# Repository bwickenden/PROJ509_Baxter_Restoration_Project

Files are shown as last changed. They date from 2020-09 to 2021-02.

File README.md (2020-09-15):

# Baxter Restoration Project

This project is to restore the Baxter robot at the University of Plymouth, to be used for research and teaching purposes. The project uses Autodesk Fusion 360 to design and tests a new gripper to repair the end effector of the Baxter robot. A Kinematics model for the Baxter has been produced, which includes both forward and inverse kinematics to be used to control the robot. Both of these systems have been used in MATLAB, with demonstrations being shown in the video folder. A Gazebo 7 simulation of the Baxter Robot was also tested during this project. The test programmes used were provided by Rethink Robots, and was used in their simulation environment. 

## MATLAB
All of the MATLAB files that have been used in the project have provided in the MATLAB folder. For all of the simulations, the vars.m and simulation.m files need to ran first. Examples of forwards, inverse kinematics and semaphore signalling are provided. 

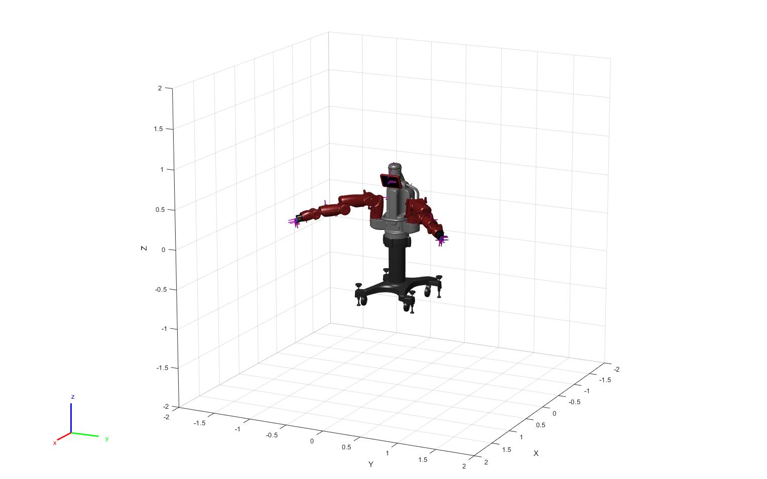
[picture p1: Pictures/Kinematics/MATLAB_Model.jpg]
MATLAB Baxter Model


## CAD

Two models for the grippers have been produced for this project. A design for both 3D printed ABS/PLA and for Aluminium has been provided. Each design has been through a sereis fo FEA tests, which concluded that each design (with its respected materials) has a minimum factor of safey above the target goal of 5. The project and stl files have beeen provided for both models. 

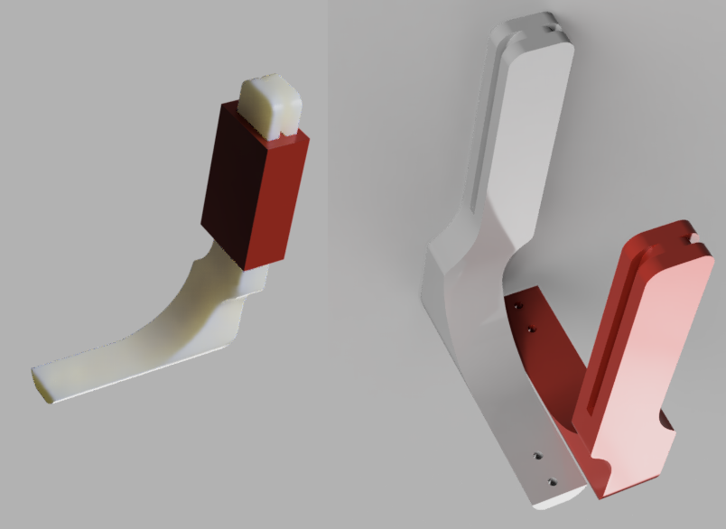
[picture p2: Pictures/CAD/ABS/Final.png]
ABS

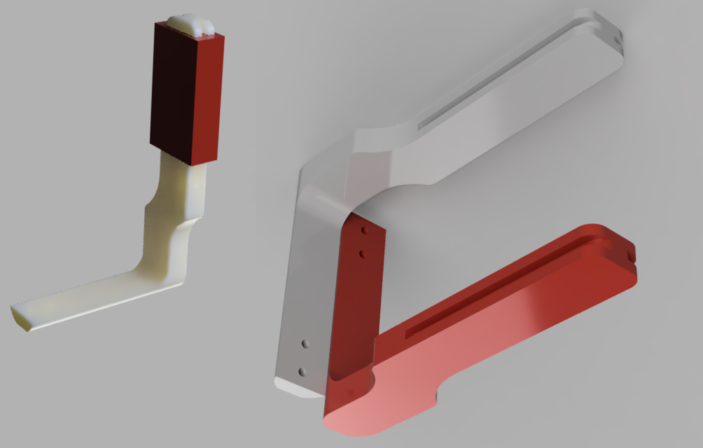
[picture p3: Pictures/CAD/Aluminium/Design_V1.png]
ALU


## ROS

Due to Rethink Robotic's workstation and  Gazebo 7 simulation using legacy software, changes has to be made to the setup of the workstation in order to get it working on Ubuntu 16.04 using ROS Kinetic. 

To set up the workstation the wiki provided by Rethink was followed and adapted. The original guide can be found at https://sdk.rethinkrobotics.com/wiki/Workstation_Setup  and the simulator guide can be found here https://sdk.rethinkrobotics.com/wiki/Simulator_Installation 

As a prerequisite an installation of Ubuntu 16.04 with ROS Kinetic is required. And to have 

### Install the SDK for Baxter 
$ cd ~/ros_ws/src
$ wstool init .
$ wstool merge https://raw.githubusercontent.com/RethinkRobotics/baxter/master/baxter_sdk.rosinstall
$ wstool update
$ source /opt/ros/kinetic/setup.bash

$ cd ~/ros_ws
$ catkin_make
$ catkin_make install

$ wget https://github.com/RethinkRobotics/baxter/raw/master/baxter.sh
$ chmod u+x baxter.sh

$ cd ~/ros_ws
$ gedit baxter.sh

In the baxter.sh file, in order for the workstation to be used within a simulation the baxter_hostname has to set to “my_computer.local”, however if the user wants to interact with the physical Baxter robot rather than the simulation, the variable “your_ip” needs to be set to the workstations ip address. Additionally, the variable of ros_version, needs to be set to “kinetic.

$ cd ~/ros_ws
$ . baxter.sh

After this the Simulator can be installed. 
With the simulaor setup a variety of test programmes can be used to experiment with

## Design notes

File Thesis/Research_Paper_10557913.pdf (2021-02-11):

## Restoration of the Baxter Robot for Research and Teaching

Benjamin Wickenden

The University of Plymouth Benjamin.wickenden@postgrad.plymouth.ac.uk

Abstract

This paper covers the restoration of the Baxter Robot project at the University of Plymouth, which ended in 2016. This includes an in-depth look into the Baxter robot and surrounding field, which incorporates topics such as teleoperation, robot-human interaction, robotics arms, industrial robotic and domestic-home robotics. As part of the Baxter robot’s restoration a replacement end effector has been designed using Autodesk Fusion 360. The design underwent a series of structural analysis tests in the form of finite element analysis (FEA) simulation software, which concluded that the models designed could endure the stress testing, whilst retaining a factor of safety above five. A simulation in MATLAB is used to show the full range of Baxter’s arms in 3D. Additionally, a 2D representation can be seen, mapping all the possible end effector positions of one of Baxter’s arms. Additionally, the inverse kinematics are also derived and demonstrated in a simulation in MATLAB. The project also used the Rethink Robotics ROS Baxter robot simulator carry out interactive testing with the Baxter robot using the keyboard. Lastly, an interactive programme in MATLAB was used to carry out semaphore signalling, which was used to spell out Baxter, when the user inputted the characters. The paper then concludes that the Baxter robot retains a lot of value for research and teaching purposes and that the project provides a starting point for future projects to continue from.

Keywords

Baxter, Kinematics, Semaphore signalling, MATLAB, Simulation, Autodesk Fusion 360, Finite Element Analysis (FEA), Human-Robot Interaction, Industrial Robotics

### 1. Introduction

The overall focus of this project is the restoration of the University of Plymouth’s Baxter Robot (Robots IEEE, 2020a), which has been out of use since 2014 and due to researcher’s departure and damage sustained. The Baxter robot is designed to for a variety of purposes including object identification, light assembly, material handling. The Baxter robot has two industrial robotic arms with 7 degrees of freedom each, with compliant joints which have force sensing capabilities, a 360o
-sonar detection
sensor, and 3 cameras (Rethink Robotics, 2012). The University’s Baxter robot has a damaged end effector which needs replacing and requires, software to be provided to interact with the robot in order for future research to be carried out. Therefore, the overall goal of this project is to restore the Baxter project to the point where research using the robot can once again take place at the University of Plymouth.

The first objective involves designing a new replacement end effector which can be 3D printed and fitted to Baxter robots’ arm. Autodesk Fusion 360 was used to create 3D CAD models of the end effectors grippers, and to carry out structural analysis on the models in the form of finite element analysis (FEA) which provided me a level of confidence with my design when experiencing extreme forces. The second objective involves creating an environment with MATLAB and ROS where a physical and mathematical model of the Baxter Robot is present and ready for testing. Which includes providing instructional documentation for installing Rethink Robotics simulator, which uses legacy software, on the University’s system. Additionally, for the MATLAB aspect of this objective, the focus is on providing the kinematics of the Baxter robots arm and the robots parameters. Objective three is focused on using MATLAB and ROS to interact with the Baxter robot. In ROS, the goal is to interact with Baxter’s arms in a Gazebo 7 simulation and the MATLAB implementation to focus on demonstrating the kinematics of the Baxter using the MATLAB robotics toolbox and to provide an interactive semaphore signalling simulation. Lastly the fourth objective is to provide additional project ideas and uses for the Baxter robot to be used in future research projects at the University of Plymouth.

The code for both the MATLAB and the ROS simulations that were carried out during the project can be found on the projects GitHub repository: https://github.com/bwickenden/PROJ509_Baxter_Restoration_Project.git along with other documentation and results. The ROS simulations were carried out in a virtual machine boot of Ubuntu 16.04, using ROS Kinetic and the MATLAB simulations were running of MATLAB R2020a.

### 2. Background Literature

### 2.1. Industrial Robots

In 2015, Rethink Robotics released the Sawyer robot, which was the successor of Baxter (Robots IEEE, 2020b). The Sawyer robot has a singular industrial robotic arm with seven degrees of freedom and has two integrated cameras, along with built in force sensing capabilities (Rethink Robotics, 2019a). Sawyer is designed to carry out pick and place tasks as well as specific manufacturing task such as CNC machining, injection moulding, circuit board assembly, and packing, along with many other tasks (Rethink Robotics, 2019b). With Sawyer’s force sensing capabilities, it allows Sawyer to carry out task carefully, by monitoring both the torque and position of each of its servos individually and simultaneously (Rethink Robotics, 2019c). By doing this it allows the robot to monitor and control the amount of force that it is applying to its target. With this ability, the Sawyer robot is able to carry out tasks within a sensitive environment, where a regular industrial robot arm, without force feedback capabilities would not be able to operate within safely. This is a similar trait that the Sawyer robot shares with its predecessor, the Baxter robot, that also made use of compliant joints with force sensing, to operate within its environment safely (Rethink Robotics, 2012). One difference between Sawyer and Baxter robot is that the Sawyer robot is less bulky and is instead flexible and streamlined to enough to work in environments which may be difficult for its human counterparts to operate within (Rethink Robotics, 2019a). This is achieved with the application of Rethinks Robotics’ Inertia Software and advanced embedded vision system, which allows for the Sawyer robot to reorient its position into a dynamic pose to suit the operational environment (Rethink Robotics, 2019b).

### 2.2. Cooking Robots

In a research study carried out by Zhai, J. et al., (2015) they simulated a dual arm, 6 degree of freedom robot to carry out Chinese cooking methods, with the idea of providing quality dishes autonomously, without the need of a master chef. In the paper, they focus on the action required to flip food within a wok, which is achieved with the use of inverse kinematics and dynamic equations, which are provided by the Lagrangian method, which calculates the Kinect and potential energy of the arms. In a study ran by Petit, A, et al., (2017), they were able to train a robot to make a pizza. This was achieved by using an RGB-D 3D camera to create a point cloud, which enables the robot to track elastic deformable objects that are textured, such as pizza dough. The unique aspect of this research is that unlike other research projects this deals with handling non-rigid objects, whereas most research appears to be in the handling of rigid tools.

### 2.3. Human-Robot Interaction

In a study carried out by Li, C. et al., (2020) they used force sensing with a KUKA LBR iiwa robotic arm to provide a massage to the user. The idea behind the project was to provide the service without the need of a person being present and to design a system that would allow for the robot to provide the massage dynamically to suit different users. With the robot being able to autonomously complete its tasks without being controlled by another person, it allows for the robot to be applied to a home robotics setting, such as a smart home. Whilst a massage for many is a luxury, for some people it may be required due to healthcare reasons and therefore this provides an important solution to this service.

### 2.4. Teleoperation

One example of teleoperation is using robots to work from home; this is achieved by a company in Japan called OryLaboratory, which has created a service robot that can be remotely controlled named the OriHime robot (OryLaboratory, 2020). In 2018 OryLaboratory conducted a trial in a café in Tokyo called Dawn Ver Café, where the service was provided by robots controlled by people with disabilities which prevented them working, via teleoperation with the goal of allowing them to remain independent (Steffen, 2020). The robot interface to control the OriHime robots has been designed to be interactable for people who have ALS and are paralyzed, which is achieved by the use of eye control, body language and simple gestures (OryLaboratory, 2020), (DAWN, 2020).

### 3. Theory

### 3.1. Kinematics

Both inverse and forwards kinematic were developed for the project. The main difference between inverse and forward kinematics is the control inputs. For inverse kinematics the user would input the target location and the model will produce the values for the joint angles in order for the pose of the robotic arm to position its end effector within the target location.
Forward kinematics allow for the
user to use the joint angles of the
robotic arm as the input controls, where the kinematic model is then used calculate the pose of the robot and the resultant location of the end effector within the environment. In figure 7, I have used MATLAB’s
robotics | toolbox | (MathWorks,
2020) to calculate all of the possible positions of the end effector within Baxter’s workspace using forwards kinematics as seen in Figure 1.

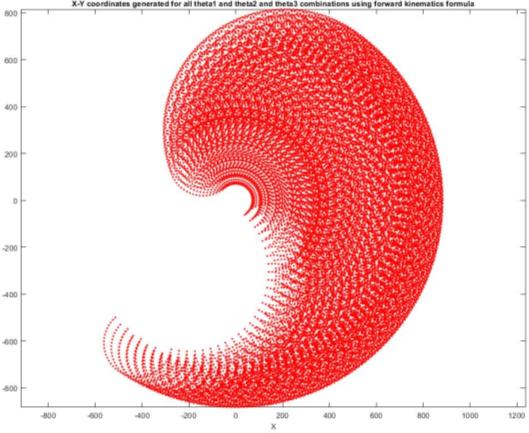
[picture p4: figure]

Figure 1: Baxter End effector range 2D

Similar to the forwards kinematics, the inverse kinematics (Equation 1) were also successfully demonstrated using a model of Baxter with MALAB, with the user inputting the target coordinates. Inverse kinematics are useful when integrated with an autonomous system, as they allow for the user to input the target location of the end effector and for the robot to provide a solution for the joint angles. However as discussed, over or undershoot may cause issue when using an open loop system with forwards kinematics, which is why a closed loop feedback system is preferred to maintain accuracy.

X =

Px
Py
φ

=

a1c2 + a2c12 + a3c123
a1s1 + a2s12 + a3s123
θ1 + θ2 + θ3

Equation 1: Where Px and Py represent the chosen x,y coordinate and a1,a2,a3 are lengths 1,2,3 with s and c representing sin and cos of angles 1,2,3

### 4. Design

### 4.1. CAD

The design for the replacement end effector offered different variants for the use of aluminium and ABS/PLA. Both designs are similar; however, the ABS/PLA design has more material added to provide a better distribution of force along the bend. There are two different designs due to the difference in the material properties between ABS and aluminium. ABS has a Youngs modulus of 1.1-2.9GPa when 3D printed (igem, 2015), whereas aluminium’s has a Young’s Modulus of 69Gpa of (The Engineering ToolBox, 2003). Both designs went through FEA with a force of 35N applied, where the results can be seen in Figure 2. The minimum factory of safety for the ABS/PLA design was 5.501, and the minimum factor of safety for the aluminium design with the same constraints and forces applied was 15, which more than exceeds target factor of safety of 5.

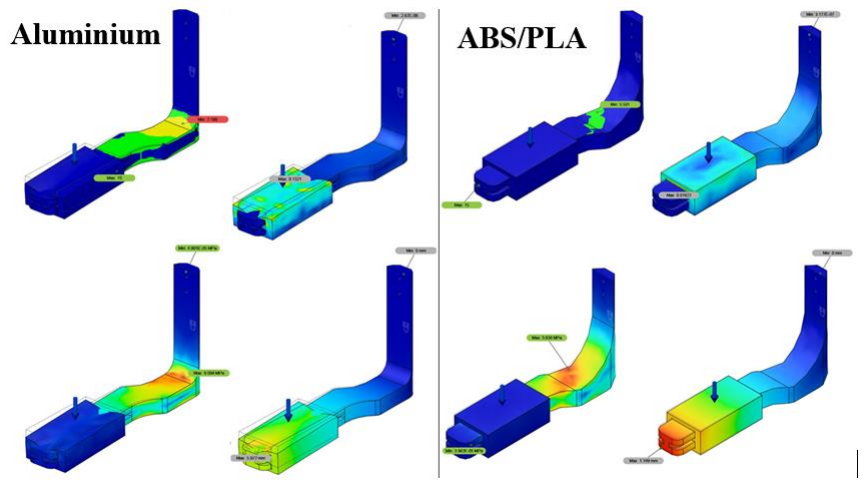
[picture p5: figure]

Figure 2: FEA Safety Factor (TL), Strain (TR), Stress (BL), Displacement (BR)

### 4.2. Semaphore Signalling

Semaphore signalling is a system designed by the Chappe brothers in the 18th century (Centre of Innovation in Mathematics Teaching, 2006) and is a method of using two flags to signal letters by the position of the user’s arms when holding the flags. Using the forwards kinematic model in MATLAB, an interactive programme was made, where the user could input the characters to spell Baxter, which results in Baxter producing the semaphore signal using his arms, seen in Figure 3.

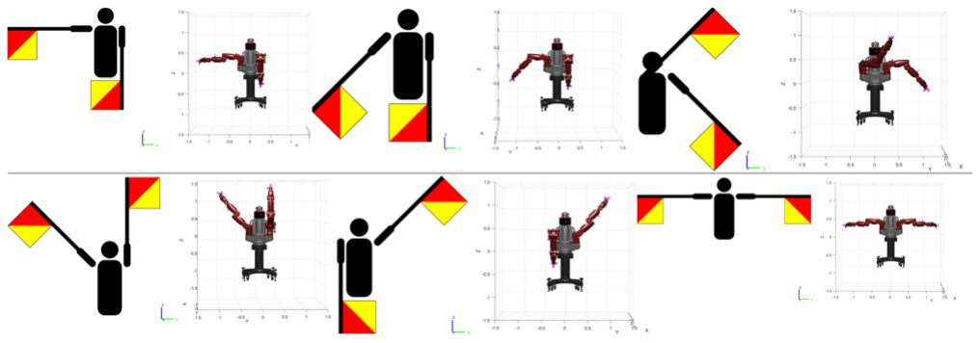
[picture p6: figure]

Figure 3: Semaphore signalling, Row 1: B, A, X. Row 2: T, E, R.

### 5. Discussion and Analysis

### 5.1. CAD

Whilst providing a structurally strong and stable part of a certain quality is important to ensure the grippers of the end effector will not require constant replacement; it is also important to consider the forces that would be applied to the rest of the robot if the end effector experiences a large impact force. With the Baxter robot’s servos costing more than a replacement gripper it is perhaps best to design the gripper to break at a predetermined threshold, which would allow for the gripper to be used within normal operation without issue, but would break when experiencing extreme force, in order to protect the servos and their gear boxes. Whilst ABS/PLA are cheaper materials that Aluminium, they are not suited to all scenarios. For example, with the print bed temperature being around 72⁰C for PLA (igem, 2015), PLA is not suited for use in hot environments. If the PLA gripper was to be used in a cooking environment, the gripper may experience damage due to heat, whereas the aluminium will be able to sustain more heat and may be better suited.

### 5.2. Kinematics

The kinematics derived and demonstrated within this project show examples of both forwards and inverse kinematics. For the purposes and scope of the project the kinematics are purely theoretical and demonstrated in a perfect system, and therefore don’t fully represent a real system. In a real system, such as using the kinematic model with the physical Baxter robot, the servos would not be perfect and therefore the location of the end effector within a 3D plane may experience some compound drift. Due to experiencing drift the certainty of the end effectors position would decrease, however a solution to this could be solved using a closed loop feedback control system. The implementation of a closed loop feedback control system can be used to increase the accuracy of the end effector by providing feedback data which will allow for adjustments to be made to the joint angles of the servos to reach the required goal. Several methods could be used as a solution this issue including a simple proportional-integral-derivative controller (PID controller) or a Kalman filter.

### 5.3. Interaction

The current semaphore signalling programme has Baxter produce the signals using his arms alone, without the use of flags. With access to Baxter, further research could be carried out with Baxter interacting with a set of signalling flags, where a project could be centred around using Baxter as a translator from variable or written commands to semaphore signalling. It is also possible that with the use of computer vision that Baxter could be taught to read semaphore signals, to then be used as input commands. In order to do this Baxter would need to make use of RBG-D camera to track the skeletal data of a user which could then be used with a machine learning programme to match the data with predetermined poses (Win, S. et al., 2020).

### 6. Conclusion and Future Work

In future I would like to carry out a series of tests using the actual Baxter robot to further the semaphore signalling system developed within the project. In a future study I would like to train the Baxter robot to recognise a semaphore signal and to be able to repeat the signal. This would be achieved with the use of a depth camera which could be used to carry out skeletal tracking of a human producing the signals. With the skeletal data recorded, the data could be converted to forwards kinematics for Baxter to replicate to reproduce the same signal. Baxter could also use the values of the joint angles to identify the semaphore signal, and thus translating the signal. A similar experiment was carried out using the pepper robot by Tian, N. et al., (2018), where they used cloud computing to mirror semaphore signals.

Due to Baxter’s compliant joints and with the use of torque sensors, which allow him to work safely with humans, Baxter has the possibility carry out cooking related tasks. Using machine learning and neural network applications, Baxter could complete kitchen tasks autonomously. A user can control Baxter via teleoperation to complete cooking tasks. This could be used in combination with a VR headset, allowing the user to see the environment fro m Baxter’s perspective (Lipton, J.I. et al., 2018). The user could then input movements using VR controllers in combination with Baxter’s torque force sensing to ensure that the appropriate force is being used to complete tasks such as cutting fruit or gripping a saucepan.

Overall, to conclude the project has successfully achieved its goals of restoring the Baxter robot project. Following the literature review of the Baxter robot and surrounding fields, it was concluded that Baxter has a lot of potential to be used for research into areas which involve robots-human interaction. It was also established that due to Baxter’s multidisciplinary potential, he also provides a valuable platform to teach students several applications of robotics. Future research into Baxter using semaphore signalling and completing cooking tasks looks promising. With the conclusion of the project, the first steps towards Baxter’s restoration have been completed, with a toolbox provided as a footing for future research to be conducted.

### 7. References

Centre of Innovation in Mathematics Teaching (2006) Semaphore. Available at: http://www.cimt.org.uk/resources/topical/semaphore/semaphore.htm.(Accessed: 13 September 2020).

DAWN (2020) Freedom for everyone to participate in society and work with their peers. Available at: https://dawn2019.orylab.com/ (Accessed: 13 September 2020).

igem | (2015) Comparison | of | typical | 3D | printing | materials. | Available | at:
http://2015.igem.org/wiki/images/2/24/CamJIC-Specs-Strength.pdf (Accessed: 13 September 2020).

Li, C. Fahmy, A. Li, S. and Sienz, J. (2020) “An Enhanced Robot Massage System in Smart Homes Using Force Sensing and a Dynamic Movement Primitive”. Front. Neurorobot. 14:30. doi: 10.3389/fnbot.2020.00030

Lipton, J. I. Fay, A. J. and Rus, D. (2018) "Baxter's Homunculus: Virtual Reality Spaces for Teleoperation in Manufacturing," in IEEE Robotics and Automation Letters, vol. 3, no. 1, pp. 179-186, Jan. 2018, doi: 10.1109/LRA.2017.2737046.

MathWorks (2020) Simulate Joint-Space Trajectory Tracking in MATLAB. Available at: https://uk.mathworks.com/help/robotics/examples/simulate-joint-space-trajectory-tracking.html.(Accessed: 13 September 2020).

OryLaboratory (2020) OriHime. Available at: http://ces15.orylab.com/ (Accessed: 13 September 2020).

Petit, A. Lippiello, V. Fontanelli, G. A. Siciliano, B. (2017) “Tracking elastic deformable objects with an RGB-D sensor for a pizza chef robot”, Robotics and Autonomous
Systems,Volume | 88,2017,Pages | 187-201,ISSN | 0921-
8890,https://doi.org/10.1016/j.robot.2016.08.023.
Rethink | Robotics | (2019a) | Applications. | Available | at:
https://www.rethinkrobotics.com/sawyer/applications#c68. (Accessed: 13 September 2020).
Rethink | Robotics | (2019b) | Sawyer | Black | Edition. | Available | at:
https://www.rethinkrobotics.com/sawyer. (Accessed: 13 September 2020).
Rethink | Robotics. | (2012) | 'Baxter | Datasheet'. | Available | at: | https://www.allied-
automation.com/wp-content/uploads/2015/02/Baxter_datasheet_5.13.pdf (Accessed: 10 April 2020).

Rethink Robotics. (2019c) ‘Rethink Robotics® meets German Engineering'. Available at: https://www.rethinkrobotics.com/fileadmin/user_upload/sawyer/rr-blackedition-brochure_low.pdf (Accessed: 13 September 2020).

Robots IEEE (2020a) Baxter. Available at: https://robots.ieee.org/robots/baxter/ (Accessed: 10 April 2020).

Robots IEEE (2020b) Sawyer. Available at: https://robots.ieee.org/robots/sawyer/. (Accessed: 13 September 2020).

Steffen, L. (2020) Café In Tokyo Uses Robot Waiters Controlled By Paralyzed People. Available at: https://www.intelligentliving.co/cafe-tokyo-robot-waiters-paralyzed-people/ (13 September 2020).

The Engineering ToolBox (2003) Young's Modulus - Tensile and Yield Strength for common Materials. Available at: https://www.engineeringtoolbox.com/young-modulus-d_417.html (Accessed: 13 September 2020).

Tian, N. et al., (2018) "A Cloud-Based Robust Semaphore Mirroring System for Social Robots," 2018 IEEE 14th International Conference on Automation Science and Engineering (CASE), Munich, 2018, pp. 1351-1358, doi: 10.1109/COASE.2018.8560553.

Win, S. and Thein, T. L. L. (2020) "Real-Time Human Motion Detection, Tracking and Activity Recognition with Skeletal Model," 2020 IEEE Conference on Computer Applications (ICCA), Yangon, Myanmar, 2020, pp. 1-5, doi: 10.1109/ICCA49400.2020.9022822.

Zhai, J. Pan, G. Yan, W. Fu, Z. and Zhao, Y. (2015) "Dynamic analysis of a dual-arm humanoid cooking robot," 2015 IEEE 10th Conference on Industrial Electronics and Applications (ICIEA), Auckland, 2015, pp. 835-838, doi: 10.1109/ICIEA.2015.7334226.

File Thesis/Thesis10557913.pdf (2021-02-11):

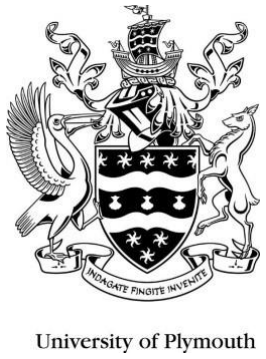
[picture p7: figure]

# Restoration of the Baxter Robot for use in Research and Teaching

# Benjamin Wickenden

### Supervisor: Dr M. Ambroze

## A thesis submitted to the University of Plymouth in partial fulfilment of the requirements for the degree of:

## Master of Science, Robotics

September 2020

School of Computing, Electronics, and Mathematics

Faculty of Science and Engineering

## Declaration

I confirm that I have read and understood the Plymouth University regulations relating to Assessment Offenses and that I am aware of the possible penalties for any breach of these regulations. I confirm that this is my own independent work.
Candidate's Signature:
<Benjamin Wickenden> | Date:13/10/2020

Supervisor's Signature:

<Dr Marcel Ambroze> | Date:

Second Supervisor's Signature:

<Dr Chunxu Li> | Date: 12/10/2020

Copyright & Legal Notice
This copy of the dissertation has been supplied on the condition that anyone who consults it is understood to recognize that its copyright rests with its author and that no part of this dissertation and information derived from it may be published without the author's prior written consent.

The names of actual companies and products mentioned throughout this dissertation are trademarks or registered trademarks of their respective owners.

## Abstract

This paper covers the restoration of the Baxter Robot project at the University of Plymouth, which ended in 2016. This includes an in-depth look into the Baxter robot and surrounding field, which incorporates topics such as teleoperation, robot-human interaction, robotics arms, industrial robotic and domestic-home robotics. As part of the Baxter robot’s restoration a replacement end effector has been designed in CAD using Autodesk Fusion 360. The design underwent a series of structural analysis tests in the form of Fusion 360’s built in finite element analysis (FEA) simulation software. The FEA testing provided an evaluation of the model which concluded that a suitable model had been produced to endure the full force of Baxter with a safety factor above five; with two different models produced, the material being 3D printed ABS, or machined Aluminium. The project also develops inverse and forward kinematics for Baxter’s arms. A simulation in MATLAB is used to show the full range of Baxter’s arms in 3D by cycling through joint angles for each of servos. Additionally, a 2D representation can be seen, mapping all of the possible end effector positions of one of Baxter’s arms. A model to demonstrate the inverse kinematics is also produced in a MATLAB simulation where the user can input the X,Y coordinates of a target location into the kinematic model which then calculates to joint angles of the servos in order for the end effector to reach its goal. The project also used the Rethink Robotics ROS Baxter robot Gazebo 7 simulation to perform interactive testing with the Baxter robot using the keyboard. Lastly, an interactive programme in MATLAB was used to carry out semaphore signalling, which was used to spell out Baxter, when the user inputted the characters. The paper then concludes that the Baxter robot retains a lot of value for research and teaching purposes and that the project provides a starting point for future projects to continue from.

## Acknowledgements

I would like to thank both Dr Ambroze and Dr Li, for their help and guidance throughout this project.

Additionally, I would also like to thank my house mates and family for their support throughout the project.

Lastly, I would like to thank all the Robotics technicians at the University of Plymouth for their time and help that they have generously provided me with throughout my time at the University.

## Contents

## 1. Introduction

The overall focus of this project is the restoration of the University of Plymouth’s Baxter Robot, which was first manufactured by Rethink Robotics in 2012 (Robots IEEE, 2020a). The University of Plymouth’s Baxter robot has been out of use since 2014 and due to researcher’s departure and damage sustained by Baxter. The Baxter robot has a damaged end effector which needs replacing and in addition, software needed to be provided to interact with the robot in order for future research to be carried out. Therefore, the overall goal of this project is to restore the Baxter project to the point where research, using the robot can once again take place at the University of Plymouth. In order to achieve this the project was broken down into four objectives.

- Design a replacement end effector for the Baxter Robot
- Have a working model of the Baxter Robot
- Provide working code to interact with the Robot
- Further experimentation

The first objective involves designing a new replacement end effector which can be printed and fitted to the Baxter robots’ arm. The main software used in the objective is Autodesk Fusion 360 which is used to create a 3D CAD model of the end effector, and is also used to carry out structural analysis on the model in the form of finite element analysis (FEA) which provided me a level of confidence with my design when experiencing extreme forces. The second objective involves creating an environment with ROS and MATLAB where a physical and mathematical model of the Baxter Robot is present and ready for testing. The ROS element of this objective also involves an instructional document which provides potential future researchers with a way to set up a ROS environment using the Rethink Robotics simulator legacy software on the University’s software requirements. For the MATLAB aspect of this objective, the focus is on providing the kinematics of the Baxter robots’ arm and the robots parameters. Objective three is focused on using ROS and MATLAB to interact with the Baxter robot. The ROS implementation involves controlling the robot’s arms in a Gazebo simulation and the MATLAB implementation to focus on demonstrating the kinematics of the Baxter robot using the MATLAB robotics toolbox. Lastly the fourth objective is to provide additional project ideas and uses for the Baxter robot to be used in future research projects at the University of Plymouth.

Due to the global pandemic of COVID-19, the direction of the project changed from its original objectives. Originally the project was to be more focused on running a full diagnostics test and repair on the University’s Baxter robot, followed up with the running of simple physical testing, which would include the robot interacting with the environment around it. However, due to the pandemic and the closure of the University’s campus on 16th March 2020, the goals and objectives of the project had to be adapted to compensate not having access to the robot and thus the project moved towards a theoretical and simulation based project, which places a greater emphasis on the literature and fields surrounding the Baxter robot.

Throughout the project, careful planning and management took place using a series of Gantt charts which allowed me to breakdown all my work packages into smaller, more manageable tasks. Over the duration of the project three iterations of the Gantt chart were produced. The original Gantt (Appendix 1), was produced pre-Covid-19 and outlined my original project plans before the University’s closure. Upon the closure of campus, the project plan was revaluated to match the new direction of the project. The new Gantt chart removed several tasks from the project plan as with the project being mainly theory based, some of the tasks were no longer possible and due to the circumstances, some tasks were no longer able to be realistically achieved within the time frame. In addition, the deadlines for work packages were pushed back by a week, due to unforeseen deadlines changes for semester two which meant that I started working on the project a week later than expected (Appendix 2). In this update of the Gantt chart I also changed how I staggered some of the tasks, by setting some tasks to run over a longer period in parallel to other tasks. This adaptation was made to allow me to work on related tasks simultaneously, which in practice helped greatly when it came to problem solving. The finial iteration of the Gantt chart is seen in (Appendix 3), which is updated due to the change in deadline, which allowed for a final adjustment of remaining tasks to be completed. The final Gantt chart is also a representation of how the project played out, rather than a forecast and therefore lends itself as a way to evaluate, time and project management skills, throughout the duration of the project.

The code for both the MATLAB and the ROS simulations that were carried out during the project can be found on the projects GitHub repository, along with video demonstrations and
CAD | files: | https://github.com/bwickenden/PROJ509_Baxter_Restoration_Project.git
Documentation on the project was also kept locally as well as on the OneDrive. The ROS simulations were carried out in a virtual machine boot of Ubuntu 16.04, using ROS Kinetic. In addition to formal documentation I also kept a paper journal which was used to planning tasks, note taking, rough mathematics and evaluation at the time of experimentation.

## 2. Literature Review

Abstract

In this literature review I will be looking into the current applications and research areas in relation to the Baxter robot focusing on areas of research and for teaching purposes. Following this, an analysis into the field surrounding the Baxter robot is carried out, starting with what other robots and robotic arms are available, that are within similar fields and scope of the Baxter robot. This paper then leads into an in-depth look into the field of home robotics and how some applications could help to tackle issues that come about due to a pandemic. The topics discussed include: Care robots, cooking robots, robot-human interaction and work from home robots, with each being linked to how they could apply to Baxter. The paper concludes that Baxter, whilst old, is yet to become obsolete, due to the assortment of hardware which allows him to be used to carry out research into robots working within the same environment as humans, in addition to his more traditional tasks.

Introduction

My research project is based upon the restoration of the Baxter robot that is currently at the University of Plymouth. The Baxter robot is designed to for a variety of purposes including object identification, light assembly, material handling. The Baxter robot has two industrial robotic arms with 7 degrees of freedom each, with compliant joints which have force sensing capabilities, a 360o
-sonar detection sensor, and 3 cameras (Rethink Robotics, 2012). With this assortment of sensors and actuators the Baxter robot has a large variety of potential capabilities. The robot has the potential to be used in research areas ranging from object identification, pick and place, human interaction, robotics in a home environment, robot-human interaction, machine learning and many more.

A feature that makes the Baxter robot interesting is that it’s been designed to operate in an environment without a protective cage around it. Most industrial robotic arms need to be out of reach of humans and confined within their own personal workspace. As part of the Baxter robots design, they implemented a system which utilises its force sensing ability, series elastic actuators, and cameras to detect or prevent robot-human collisions (Fitzgerald, C. 2013). With this ability it places the robot in an unusual category as it has the potential to be used in home like environments, whilst still having the capabilities of an industrial robotic arm. With research into home robotics increasing in popularity, the Baxter robot could be used to investigate the viability of cooking, cleaning, and other domestic tasks.

With the Baxter Robot being first produced in 2012 by Rethink Robotics (Robots IEEE, 2020a), the Baxter has been involved in many research projects since. One of the projects involved an advanced telecommunication system using an MYO armband which has 8 inbuild EMG sensors accompanied by a 9 axis IMU, to allow the user to control the Baxter robot with the movements of their own arm (Yang, C. et al. 2016). Additionally, another project made use of a mobile robot to further increase the safety of the environment when the Baxter is operational. The research team created a warning system which implemented an Xbox Kinetic camera sensor on the mobile robot which would survey the area within the Baxter’s range. When a human gets closer to Baxter, it would alert them that they have crossed one of the three thresholds of safety ranging from safe (+3m), caution (3m), danger (1.5m), and emergency stop (1m) (Reardon, C. et al 2015). Despite the robot now approaching 8 years old the Baxter robot is still being used in research projects and has a lot of potential as a tool to pioneer modern day robotics which is explored throughout this paper.

Industrial robots

In recent years Rethink Robotics have developed the successor of the Baxter Robot, named the Sawyer Robot, which was released in 2015 (Robots IEEE, 2020b). The Sawyer robot has a singular industrial robotic arm with seven degrees of freedom and has two integrated cameras, along with built in force sensing capabilities (Rethink Robotics, 2019a). Sawyer is designed to carry out pick and place tasks as well as specific manufacturing task such as CNC machining, injection moulding, circuit board assembly, and packing, along with many other tasks (Rethink Robotics, 2019b). With Sawyer’s force sensing capabilities, it allows Sawyer to carry out tasks carefully, by monitoring both the torque and position of each of its servos individually and simultaneously (Rethink Robotics, 2019c). By doing this it allows the robot to monitor and control the amount of force that it is applying to its target. With this ability, the Sawyer robot is able to carry out tasks within a sensitive environment, where a regular industrial robot arm, without force feedback capabilities, would not be able to operate within safely. This is a similar trait that the Sawyer robot shares with its predecessor, the Baxter robot, that also made use of compliant joints with force sensing, which allowed it to operate within its environment with increased levels of safety (Rethink Robotics, 2012). One of the big ways in which the Sawyer robot is not similar to the Baxter robot is that the Sawyer robot is less bulky and is instead flexible and streamlined to enough to work in environments which may be difficult for its human counterparts to operate within (Rethink Robotics, 2019a). This is achieved with the application of Rethinks Robotics’ Inertia Software and advanced embedded vision system, which allows for the Sawyer robot to reorient its position into a dynamic pose to suit the operational environment (Rethink Robotics, 2019b).

Another example of an industrial robotics arm which is designed to work alongside its human counterpart within the workplace environment is the LBR iiwa robotic arm developed by KUKA which was first released in 2013 (Robots IEEE, 2020c). Much like the Baxter and Sawyer robot the LBR iiwa robot also makes use of compliant joints with torque sensors, which measure any external forces that are acting on the robot to prevent injury to itself and others. This is to once again ensure safe operation when around humans, also making sure that the force being exerted by the robot is appropriate for the task at hand, as the robot may be operating with delicate or dangerous materials (KUKA, 2017). Similar to the Baxter and Sawyer robots, LBR iiwa is also capable of carrying out complex tasks including but not exclusively: machining, inspection, assembly, as well other tool task such as paining and gluing surfaces (KUKA, 2020). In addition, the LBR iiwa robotic arm also has the ability to attach a variety of media flanges which allows the robot to interact with its environment in diverse ways. This includes electric/IO/touch/inside electric media flange, pneumatic/IO/touch/IO valve/inside pneumatic media flange, and the basic flange. With a large variety of media flanges, the LBR iiwa robot is able to carry out a large number different and distinct tasks, but it also allows the user to interact with the robot in a versatile way (KUKA, 2017).

Robot-enhanced Home Automation

With the Baxter robot being designed to operate within an environment without being placed within a safety cage, research can be carried out using the Baxter robot to further develop the field and our understanding of areas such as human-robot interaction and home robotics (domestic robotics). Safe interaction between robots is becoming increasingly important with more robots and robotic devices being in consumer home than ever before (Sahi, M, 2020). With advancements in the field of home robotics, robots are now able to carry out tasks and services which would have previously required a person to carry out. This is now, more important than ever during the COVID-19 pandemic, where social distancing has become a key and important part of everyone’s lives for a prolonged period of time. During the pandemic mitigating the amount of people that you come into contact with and interact with is essential for the safety yourself and others around you. With the application of home robotics, in areas such as care, cleaning and cooking. Additionally, robots could be used to allow users to carry out their jobs from the safety of their homes during the current pandemic via teleoperation.

I. Care Robots

The need for care robots in the future has been identified by governing bodies around the world, such as the United Kingdom’s government, which predicts by 2040, around a seventh of its population will be aged 75 or over and that they have identified that autonomous care robots are part of the solution to providing the nation with effective care (Department for Business, Energy & Industrial Strategy, 2019). One of the robots that the Government of the United Kingdom recognised as an already suitable robot to carry out care activities and responsibilities is the Pepper robot, which is a humanoid robot created by Softbank Robotics (Robots IEEE, 2020d). The Pepper robot is designed to be a social robot, with robot-human interaction being its primary feature, with Pepper having speech recognition for 15 languages, and a perception module which allows Pepper to recognise and interact with people. In addition, Pepper has a total of 20 degrees of freedom which allows it to carry out expressive movements which look natural (SoftBank Robotics, 2020b). Within the care industry Pepper could fulfil a role as a robot companion, with the use of its’ social abilities which allows it to communicate positively to patients in care, whom may spend extended duration of time alone (SoftBank Robotics, 2020c). Also, Pepper can assist patients to self-diagnose health issues and can be used to monitor and track on going health issues (SoftBank Robotics, 2020a). By having a robot such as Pepper carry out assistive medical care, medical staff are required for fewer visits or a shorter period or time for simple, but time-consuming tasks can be offloaded to an autonomous robot. With the use of teleoperation, carers and medical staff can also operate the Pepper robot to carry out telemedicine tasks, which allows them to interact with the patient remotely and due to Peppers interactive chest display, which allows for visual interaction(SoftBank Robotics, 2020b) (SoftBank Robotics, 2020a).

Another example of a care robot is the Robear which is another humanoid robot designed to be used in a care situation (Riken, 2015). The main use for Robear is to assist patients who are for example wheelchair bound to move between their chair and their bed (Gallagher, A. et al., 2016) (Johnson, M.J. et al., 2017). The Robear has two robotics arms which it uses to perform a lift action upon the patients and utilises torque sensors alongside capacitance-type tactile rubber sensors which allows for the robot to interact with the patients safely, without causing harm (Riken, 2015). Whilst the Robear robot cannot work autonomously and does require the aid of carer or medical professional, it does allow for the patient to be moved with ease without the need for the carer to exert themselves, especially if the patient requires to be moved on a regular basis.

II. Cooking Robots

With it becoming more normal for robots to carry out menial tasks within the household, we can now start to see the idea of having a cooking robot that can autonomously prepare and cook meals within a household. By having a cooking robot installed within the home it could allow for people who live busy lives to be able to still eat nutritional and healthy food, without the time commitment required to usually cook meals. Also, a home cooking robot could also benefit someone who is not able to cook due to illness, health related issues and the elderly. With many countries, such as Japan (Wada, K. et al., 2013) now having an aging population, allowing the elderly to maintain their independence is going to become an essential part of the future and having cooking robots to allow them to have healthy home cooked meals prepared for them could be part of the solution (Ma, W.-T. et al., 2011), (Pearce, A.J. et al. 2012)

An example of a home cooking robot is the robot kitchen designed by Moley Robotics (Moley Robotics, 2020a). Moley’s robot kitchen is comprised of a workstation which contains a stove, oven and food prep area, which the robotic arms can interact with autonomously. The robot kitchen makes use of a library of recipes which it can cook, when the given ingredients are provided and placed within the correct areas. The robot kitchen also has an option for the user to create their own recipes for the robot to re-create. This is achieved by making use of a 3D camera which tracks and records the user’s skeletal kinematics whilst they cook, which can then be later replicated by the robotic arms. In order for the user to interact with the cooking robot an interactive touch screen is provided as part of the workstation, as well as a mobile application which allows the user to interact with the robot kitchen (Moley Robotics, 2020b). A similar example of this style of cooking robot can be seen produced by companies Samsung, with their Bot Chef, which works as a kitchen assistant alongside other human chefs (Samsung Newsroom, 2019) (Teachable, 2019).

Connected Robots is another company that has been developing several robots to carry out a variety of tasks within the kitchen. Their list of robotic systems include the following: OcotChef A robot designed for baking), Soft Cream Robots (An ice cream serving robot), HotSnack Robot (A fast-food cooking robot), Lorine (Which is a breakfast robot), Dish Washing System I (A cleaning robot), Dish Washing System II (Cleaning), Dish Washing System III (Cleaning), Beer Serve Robot (Serving Robot), Soba Robot(Designed to cook and serve food at train stations), and Chef Collaboration (Which is an assistant chef robot) (Connected Robotics, 2015). All of the robots designed and created by Connected Robots have been designed to work alongside their human counter parts, with the goal to offload the workers from repetitive, low skill tasks, this is achieved by using 3D cameras with the implementation of AI and machine leaning.

In a research study carried out by Zhai, J. et al., (2015) they simulated a dual arm, 6 degree of freedom robot to carry out Chinese cooking methods, with the idea of providing quality dishes autonomously, without the need of a master chef. In the paper, they focus on the action required to flip food within a wok, which is achieved with the use of inverse kinematics and dynamic equations, which are provided by the Lagrangian method, which calculates the Kinect and potential energy of the arms. Another research study carried out by Inagawa, M. et al. (2020) proposes a method of recipe analysis which involves turning a cooking recipe into a series of motion codes, which can be used to control the robot. The study finds that by using a data base of motion codes, the robot is able to pick out key words within a recipe and carry out the required action autonomously. However, the database that the robot uses is complex and needs simplifying for further research and operation. Lastly, we can see that in a study ran by Petit, A, et al., (2017), they were able to train a robot to make a pizza. This was achieved by using an RGB-D 3D camera to create a point cloud, which enables the robot to track elastic deformable objects that are textured, such as pizza dough. The unique aspect of this research is that unlike other research projects this deals with handling non-rigid objects, whereas most research appears to be in the handling of rigid tools.

III. Teleoperated Robots

One example of using robots to work from home is a company in Japan called OryLaboratory, which has created a service robot that can be remotely controlled named the OriHime robot (OryLabortatory, 2020). In 2018 OryLaboratory conducted a trial in a café in Tokyo called Dawn Ver Café, where the service was provided by robots controlled by people with disabilities which prevented them working, with the goal of allowing them to remain (independent Steffen, 2020). The OriHime robots were teleoperated from the homes of the workers, where they could control the robots to collect table orders, and to deliver the customers food and drink. The robot interface to control the OriHime robots has been designed to be interactable for people who have ALS and are paralyzed, which is achieved by the use of eye control, body language and simple gestures (OryLabortatory, 2020), (DAWN, 2020). Since the trial which took place in 2018, the fast good giant MOS Burgers is now currently undertaking a new trial using the OriHime robots to allow their workers which cannot commute due to illness, to continue working (Baseel, 2020). In a paper written by members and founder of OryLaboratory (Takeuchi, K. et al., 2020) they concluded that their studies had shown that the interactions that the patients had with the robot avatars whilst working, has had a positive effect to their mental fulfilment. Additionally, the paper finds that by providing people who require care an opportunity to continue working from their homes, it allows them to remain within a care environment, whilst maintaining their independence.

Another company that is trying to pioneer the robot aided work from home industry is TELEXISTENCE, which has designed the Model H robot (TELEXISTENCE, 2018). The Model H robot is a mobile humanoid robot which has been equipped with stereo cameras, binaural mics, and haptic sensors. The robot is controlled by teleoperation by the user, which interacts with the robot using the cockpit that is provided. The cockpit is an all-in-one station which includes a virtual reality (VR) headset, Haptics gloves and display which allows the user to interact with the robot over long distances, from the robot’s perspective (TELEXISTENCE, 2019). With the use of the VR headset alongside the haptics gloves, the user is able to control the robot’s arms to interact with its environment, whilst being provided physical feedback. The robot uses a hybrid method of control where it takes the uses inputs movements in combination with an AI to best optimise the task at hand, which assists in tasks such as pick and place and grasping objects. For versatilely the robot can be connected to via variety of methods including Wired LAN, Wi-Fi, and via a mobile network, which allows the robot to be used in diverse environments (TELEXISTENCE, 2018). For example, the robot could be used to carry out dangerous task, which may pose a physical or environmental hazard to humans, however for a task of great severity a wired connection may be preferred if the robot is not required to travel any great distance and is perhaps stationary. However, on the other hand, if the robot is being used for social activities where the robot may be moving around traversing its environment, then connection over the Wi-Fi or mobile would be more appreciated, especially for longer distances.

Robot-Human Interaction

The GummiArm is a soft-robot arm developed at the University of Plymouth by Dr Martin Stoelen and is designed as an open source project with the idea that anyone could 3D print the parts from home and to assemble the arm themselves (Stoelen, F, M. et al., 2018). The GummiArm is designed to be safe for robot-human interaction and makes use of soft robotic applications to allow for both the user and the robot to remain safe when interacting with each other. The GummiArm achieves this by using agonist-antagonist joints in conjunction with a duel phase ballistic-feedback controller which allows the hand to react to sensory feedback at high speeds, which was inspired by human ballistic reactions to a sensory input (Stoelen M,
F. et al., 2016). This then allows for the arm to have variable stiffness actuation which allows for the arm to dynamically adapt to the external forces within its environment when interacting with objects or people. Not only does this protect the people around the robot, but it also projects the servos which are used to drive the robot from external forces which could damage the gears within. With the use of variable stiffness, research was able to be carried out where the GummiArm would provide shake the users hand and offer a rating for their handshake (Stoelen, F, M. et al., 2018). Another experiment carried out using the GummiArm using a Convolutional Neural Network (CNN) would be able to learn to provide a high five to a variety of users (Denoun, B. et al., 2016). In addition to robot-human interaction the GummiArm has also been heavily modified to be applied to horticulture, where the arm has been used to harvest cabbages and raspberries (Klein, F.B, et al., 2019).

In a study carried out by Li, C. et al., (2020) they used force sensing with a KUKA LBR iiwa robotic arm to provide a massage to the user. The idea behind the project was to provide the service without the need of a person being present and to design a system that would allow for the robot to provide the massage dynamically to suit different users. With the robot being able to autonomously complete its tasks without being controlled by another person, it allows for the robot to be applied to a home robotics setting, such as a smart home. Whilst providing the benefits of having a massage available to the user whenever they chose, without time constraints, within the context of the COVID-19 pandemic, this is another way in which people could continue to social distance and minimise their contact with others. Whilst a massage for many is a luxury, for some people it may be required due to healthcare reasons and therefore this provides an important solution to provide this service.

Modelling Baxter

In a study carried out by Smith, A. et al (2016), they developed a dynamic model from the Baxter robot using the Lagrange formulation. The dynamic model was used to provide the relationship between the torque of the joint actuators and the resulting motion of the joints. The torque of each joint is estimated using Baxter’s compliant joints, by measuring the spring deflection using hall effect sensors. The Lagrange-Euler formulation was then used to model the motion of the Baxter arm. With the dynamic model created, an experiment was conducted where one of Baxter’s arms was driven through a series of generated trajectories, which concluded that the system was accurate when compared to the real dynamics.

Discussion

With Baxter being a stationary robot, it is not able to perform some tasks such as a lift assist robot like Robear (Riken, 2015). However, with the use of his compliant joints, Baxter is able to work alongside its human counterpart (Rethink Robotics, 2012), Baxter is still relevant for research purposes and can be used to investigate many of the key aspects required to carry out each one of the tasks within the field discussed. In a care related field Baxter has the ability to be expressive with the use of his display screen which is attached to Baxter’s head, which would allow him to simulate emotions with eye movements in a similar way to which Pepper is able to when interacting with users. Whilst Baxter’s arms are not as complex as Peppers, Baxter still has the capability perform simple emotes with them, when interacting with others. Additionally, Baxter could be used to pass objects to patients who are bound to a bed or wheelchair.

The field of cooking robots is perhaps more suited to Baxter than care, as robots designed to cook often don’t require movement around the environment and are usually stationary. With the use of the cameras and torque measurements Baxter could be used in a cooking environment. The RGB-D cameras can be used in combination machine learning, to carry out object identification, which would allow Baxter to identify cooking equipment, such as a knife and chopping board, as well as ingredients such as an onion. Baxter could then carry out a slicing action, whilst using his torque measurements and compliant joints to ensure that the correct amount of force is being applied. This could be especially useful when interacting with more delicate foods such as eggs or meringues. Additionally, similar skills could be transferred to other cooking utility tasks such a washing, cleaning and tidying.

Similar to research carried out with the KUKA LBR iiwa arm (Li, C. et al., 2020), Baxter can use his joint torque control alongside his compliant joints to be used to perform interaction with a human user. In the same way that the KUKA LBR iiwa arm is able to provide a massage for a user, an adapted method could also be applied to Baxter, to allow him to carry out the massage task. Whilst Baxter does not have a complex end effector such as the hand seen on the GummiArm, Baxter can still provide the actions of a hand shake with its arm, Baxter can also be used to pass objects directly to a user’s hand, and perhaps with the use of computer vision and machine learning it would be possible to even have Baxter interact with the user in a social setting such as a game of chess.

Due to Baxter being able to be controlled by means of teleoperation, Baxter could be used to carry out research that would investigate was to allow workers to work from home. Teleoperation allows the user to operate the robot remotely, which allows the robot to be used in situation that are not safe for humans. An example of this could be within a lab working with hazardous materials. This could also allow people to work from home in situation such as a pandemic, where social distancing is essential.

It’s clear that whilst some progress has been made to create autonomous home robots, there is yet to be a non-specialised robot that is capable of completing a variety of tasks within the home. Further research into machine learning and neural networks is still required to provide a solution for a dynamic home robot. Whilst robots such as Baxter, Sawyer and Pepper are already able to interact with objects and people relatively safely, the software is the constraint that needs to be further developed in order to increase the functionality of the robots. Therefore, Baxter is still applicable as candidate alongside his successors and in some cases may be more suited than Sawyer, due to having two arms.

Whilst the focus of this review has leant towards the application of robots within a home environment to show the potential versatility of the Baxter robot, Baxter is still a credible robot to research industry-based tasks, and many go hand in hand with the main principles behind the home robotics application, with examples being the use of computer vision for object identification and pick and place based tasks. A task involving the use of tools in an industry background isn’t vastly different to using kitchen equipment in practice.

With the Baxter robot available at the University of Plymouth, it can provide the equipment and resources that could be used to investigate and research into all the fields discussed. In relation to teaching, it would provide students with an example of human-robot interaction and designing application to work alongside humans. Additionally, it will provide a resource for students to learn about computer vision, machine learning, ROS programming, MATLAB simulations, Kinematic, teleoperations and others. Whilst other robots at the University can be used to apply some of these teachings, few robots at the University can apply all of them and thus the Baxter robot will add value.

Conclusion

After looking into several fields of robotics within the both the industry and home setting, my literature review concludes that Baxter is still a viable robot to pioneer research into all of these fields. Whilst Baxter is some 8 years old (Robots IEEE, 2020a) and is now considered a legacy robot with the release of its successor, the Sawyer robot (Robots IEEE, 2020b), Baxter is yet to become obsolete. Due to Baxter’s ability to work alongside it’s human counterpart and having an interactive display, Baxter is a versatile robot which allows it to be multidisciplinary in the fields that it can be applied to. Whilst most current applications of the Baxter robot are focused on industrial tasks; Baxter is also suited to home robotics applications. With the market for robots within the home and industry growing the Baxter robot will be a useful asset for the University of Plymouth for both teaching and research purposes. It is also clear that more research needs to be developed and driven by academics to ensure that knowledge and technology is shared and not retained by individual companies.

## 3. Theory

### 3.1 Inverse Kinematics

Inverse kinematics is a method of describing the pose of a robotic arm derived from the target position. The main concept of inverse kinematics is that if the coordinates of the target location are known, and the parameters of the robot’s arms, in this case Baxter’s arms, also being known, then you can calculate the angles of the joints in order to reach the target position. This method is very useful in a simulation environment as the distance and coordinates to objects and target locations is easy to obtain, however in a real-life scenario Inverse kinematics can be difficult to implement and rely on application input analysis such as computer vision and SLAM. In situations where it may be difficult to obtain a useful map of the environment, forward kinematics may be more appropriate. Forward kinematics is a method of calculating the pose of the robotics arms end effector when provided with a set of angles for each joint, which is used later in the project to carry out a series of experiments.

For the inverse kinematic model, I’ve first focused on solving the 2D kinematics for one of Baxter’s arms (Yan, C., 2020) To simplify the kinematic model, we can set the orientation of the end effector φ, which will be equal to the sum of angles (Equation 1). Whilst this does simplify the model and thus limits the workspace of the Baxter robot, Baxter is still able to operate in a large area however the orientation of the arm is restricted to a 2D plane. By using a simpler inverse kinematic model, it allowed for the focus of the MATLAB simulations to tangible, with only one solution to the robots pose being provided, opposed to the serial possible solutions if the robot was not restricted to a 2D plane. Additionally, for the angle of S2 (equation 3) the positive angle was always chosen to further simplify the kinematic model to, always only provide one solution for the pose of the arm to reach the desired target.

Angles θ1, θ2 and θ2 represent the joint angles of S1, E1, W1 respectively, with lengths a1, a2, and a3 are the lengths of each section of Baxter’s arms [table 1]. Symbols c and s represent cos and sin functions of angles θ1, θ2 and θ2 as denoted by subscript. X represents the target, where Px and Py are the target coordinates in the x and y axis.

End effector orientation

φ = θ1 + θ2 + θ3 | (1)

The 2D kinematics are stated in equation 2.

X = [

Px
Py
φ

] = [

a1c2 + a2c12 + a3c123
a1s1 + a2s12 + a3s123
θ1 + θ2 + θ3
] | (2)

For θ2 in the frame of w (origin)

Pwx = Px − a3cφ = a1c1 + a2c12 | (3)

Pwy = Py − a3sφ = a1s1 + a2s12

Pwx

2 + Pwy

2 = a1
2 + a2

2 + 2a1a2c2

c2 =

P

2
wx + P

2
wy − a

2
1 − a

2
2
2a1a2

s2 = ±√1 − c
2
2

θ2 = Atan 2(s2, c2)

For θ1 in the frame of w (origin)

Substitute θ2 equation 3

s1 =

(a1+a2c2

)Pwy−a2s2Pwx
P²wx+P²
wy

(4)

c1 =

(a1 + a2c2

)Pwx − a2s2Pwy
P²

wx + P²
wy
θ1 = Atan 2(s1, c1)

For θ3 in the frame of w (origin)

φ = θ1 + θ2 + θ3 | (5)

θ3 = φ − θ1 − θ2

Now that we have solved the kinematics within a 2D plane for the Baxter robots’ arm, we now need to solve the kinematics in 3D space. This can be achieved by having the Baxter robot align itself with the same plane as the target using a rotational matrix. This will we achieved by calculating the angle of the target between the x-axis and the z-axis which can be seen in figure 1 (Equation 6). In the code this value is represented by Z0 and is used for the angle of S0.

Z0 = atan2(x, z) | (6)

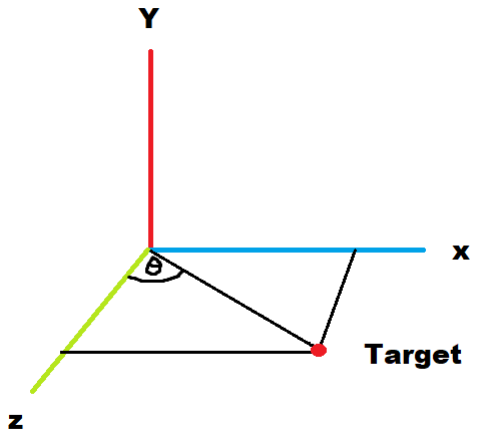
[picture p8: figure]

Figure 1: Calculating the Angle for the Shoulder Yaw Joint

With the inverse kinematic model completed, I then continued to run a series of tests using MATLAB’s robotic toolbox to visually represent the inverse kinematics generated (MathWorks, 2020b). Firstly, the inverse kinematics are calculated in the vars.m program, using the desired X, Y coordinates, which are the variables Px and Py. In vars.m the parameters of Baxter have been defined using the Rethink Robotics Baxter Manual to declare the lengths of each section of Baxter’s arms in mm (Rethink Robotics, 2015b). Once the angles of S1, E1, and W1, (which are represented by b1, b2, and b3 respectively within the code), have been calculated they are then fed into Inverse_Kinematics.m. Inverse_Kinematics.m uses the rigid body tree for Baxter provided to the tool box by Rethink Robotics (MathWorks, 2020a), which is used to visualise the pose of the Baxter robot that the inverse kinematics have computed. The function “targetJointPosition” is used to provide the robot with the inputs for all of the arm’s joint angles. In figure 2 I have the input of S1, E1 and W1 represented by the angular outputs calculated in vars.m (b1, b2 and b3). The rotational joint values of Baxter’s arm, S0, E0, W0 and W2 are defined in figure 3 and are used to set Baxter’s initial pose, where his arms are able to operate without collision with the rest of his body.

Figure 2: Inputting Inverse Kinematics into Baxter Model

Figure 3: Baxter Joint Angle Pre-sets

With the test environment set of within MATLAB, I recorded a data set containing the angles of the joints S1, E1, and W1 for incrementing Px coordinates starting from 300, incrementing by a 10 until reaching 500. For this test Py remained as the value of -300 and the start and end positions are shown in figure 4. As shown, the inverse kinematics were able to successfully move the end effector along the x-axis, to the new target coordinates. The pose shown in figure 4 is one of two possible solutions as the arm could have also take the inverse route, however for this simulation I have simplified the math, which ensure that the robot always takes the positive route rather than the negative.

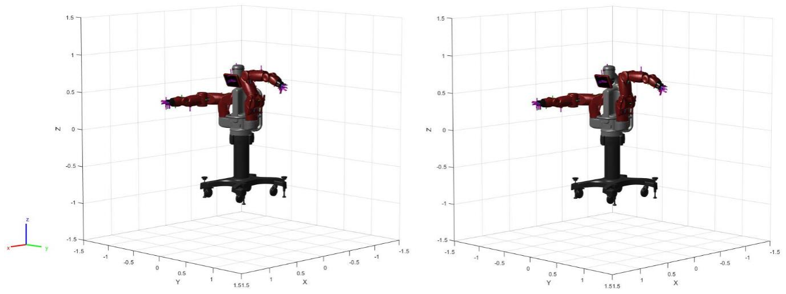
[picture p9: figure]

Figure 4: Inverse Kinematics start pose (left), finish pose (right)

### 3.2 Forward Kinematic

In addition to the inverse kinematic model I’ve also developed a forward kinematic model. The main difference between inverse and forward kinematics is the control inputs. For inverse kinematics the user would input the target location and the model will produce the values for the joint angles for the pose of the robotic arm to position its end effector within the target location. Forward kinematics allow for the user to select the joint angles of the robotic arm as the input controls, where the kinematic model is then used calculate the pose of the robot and the resultant location of the end effector within the environment. In figure 5, I have used MATLAB using the robotics toolbox (MathWorks, 2020b) to calculate all of the possible positions of the end effector within Baxter’s workspace using forward kinematics, where (0,0) represents the base Baxter’s shoulder from a side on view, with the front facing to the right. Here it can be seen that Baxter’s workspace is mainly directly in front and above its origin; with some positions allowing it to operate behind it. This shows that Baxter is more suited to operating within the environment directly in front of it and would require rotating in order to better interact with the environment behind it. Additionally, we can also see that Baxter is able to interact closely with it the environment in front and above it, however the minimum range of Baxter increases once the end effector passes 0 on the X-axis. Whereas the minimum range of the end effector increases Baxter is still able to operate directly below him and can reach areas further behind him when the location of the end effector is operating below the X-axis, in comparison to when operating above.

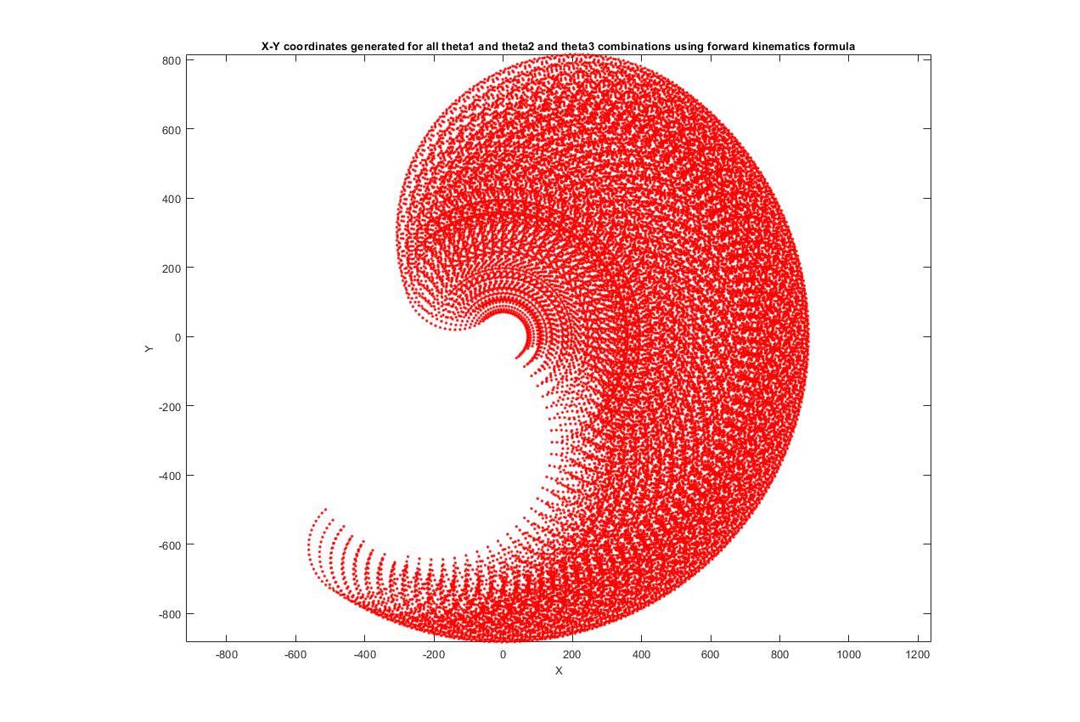
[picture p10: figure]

Figure 5: Kinematic Range of Baxter Arm

In the programme, I implemented the parameters of Baxter’s arm and set the joint angles of S1, E1, W1 to step through the entire movement range of their values as seen in figure 6 and save them into an arrays called theta1, theta2 and theta3 respectively.

Figure 6: Stepping through all values of theta

With the entire range of the angles for S1, E1 and W1 saved into arrays I then calculated the X and Y coordinates of the end effector for every arrangement of angle values figure 7, where the values of l1, l2 and l3 are the lengths of each section of the arm. I then created an array for each one of the X, Y, theta data sets, called data1, data2 and data3; which were then plotted onto a graph (figure 5). All of the parameters of the Baxter robots’ arm where from Rethink Robotics Baxter manual (Rethink Robotics, 2015b) and can be seen in table 1.

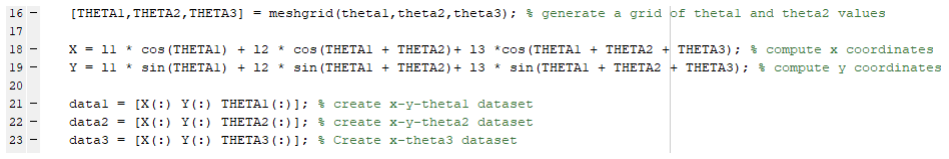
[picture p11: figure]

Figure 7: Computing X Y coordinates and datasets

Joint | Type | (Radians) Min limit | Max limit | Range | Length between joints (mm)
S1 | Shoulder Pitch | -2.147 | +1.047 | 3.194 | 364.35
E1 | Elbow Pitch | -0.05 | +2.618 | 2.67 | 374.29
W1 | Wrist Pitch | -1.5707 | +2.094 | 3.6647 | 144.895
S0 | Shoulder Yaw | -1.7016 | +1.7016 | 3.4033 | N/A
E0 | Elbow Roll | -3.0541 | +3.0541 | 6.1083 | N/A
W0 | Wrist Yaw | -3.059 | +3.059 | 6.117 | N/A
W2 | Wrist Roll | -3.059 | +3.059 | 6.117 | N/A
Table 1: Baxter Parameters (Rethink Robotics, 2015b)

With the range of each of the joint angles being defined, I carried out a simulation, called Forward_Kinematics.m, where I moved each one of the Baxter robots’ joints between its maximum and minimum joint angle individually, in the order listed in table 1. The animation shows the full range of the Baxter robot within 3D space and is controlled by inputting the angles for each of the servos individually to move the end effector. The simulation initialises with having the Baxter robots’ arms being set to a pose where both arms are facing forward whilst being outstretched figure 8.

Figure 8: Initialising joint angles

From the initial pose I then set the joint angle for S1 to its minimum angle and then stepped through the entire range of the joint incrementing by 0.1 radians until achieving the maximum value figure 9.

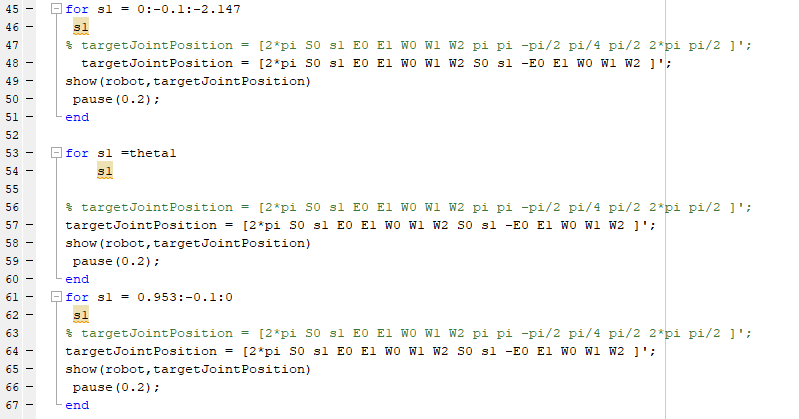
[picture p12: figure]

Figure 9: Cycling Through the All Joint Angles for S1

After achieving this, I then continued to simulate the range of the rest of the joint in a similar fashion and retuned them all back to the initialisation pose before changing joint. A section of the output from this simulation can be seen in figure 10 where the Baxter robot is cycling through the range of angles for S1, where the figure on the left show the initialisation pose and the figure on the right shows the max value of S1.

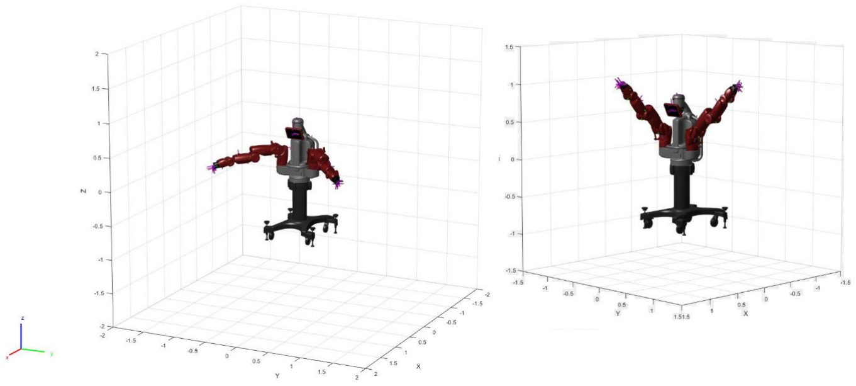
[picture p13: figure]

Figure 10: Forward Kinematics 3D Environment

## 4. Design

### 4.1 End effector

For this task I’ve used Autodesk fusion 360 to model a replacement end effector to be attached to the Baxter robot, whilst using Rethink Robotics Electric Gripper Installation manual to acquire the specifications and dimensions (Rethink Robotics, 2015a). In order for the gripper to operate correctly I had to ensure that the design would allow for each of the end effectors to move parallel to one other without colliding. At the same time, it is also essential that whilst achieving this, the gripper also remained aligned in order for the gripper to functionally hold an object within its grasp. The first iteration of the design is shown below in figure 11. The gripper portion of the end effectors have a track which goes down the centre of the outside edge of the model. This allows for a variety of attachments to be fitted to the gripper, one of which being a rubber block which provided a suitable surface material for the gripper to use to interact with objects. The design incorporates two 3mm holes which allows the gripper to be fitted to the Baxter robot using hex screws. And the total length of the grippers base is 80mm which is a mid-size variant according to Appendix 4. Due to how the design of the base has been carried out, it would be very easy to adjust the length of the base to create the additional variations of the gripper to allow for operation of the Baxter robots entire range.

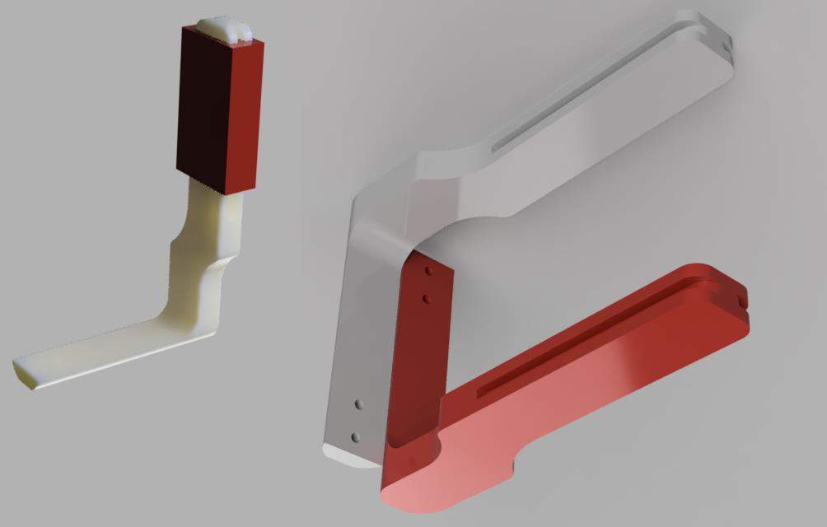
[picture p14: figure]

Figure 11: End Effector Initial Design

With the initial design completed I wanted to test the design to see if it was structurally safe when under the full force of the gripper. In order to achieve this, I ran a series of finite element analysis (FEA) tests to determine this. Firstly, I selected the material for the main body of the end effector to be acrylonitrile butadiene styrene (ABS) as it is the closest material to polylactic acid (PLA), which would be my preferred choice. The reason for this is that I wanted the design to be 3D printable using the University’s facilities and PLA is the most readily available material. PLA when 3D printed has a Young’s Modulus of 3.5GPa, where ABS has a Youngs Modulus of 1.1-2.9GPa when 3D printed (igem, 2015). Due to ABS having a smaller Youngs Modulus the forces that the model can withstand should not cause an issue with using PLA in its place. The material for the rubber attachment was chosen to be silicone rubber. The material properties for the attachment are not significantly relevant to the tests, as they are evaluating the structural integrity of the model, whereas the material for the contact piece is more relevant to surface friction and the end effectors ability to grip and object.

With the material parameters defined, I set the base of the gripper as the constraint and placed a 35N linear load onto the end effector, acting on the rubber attachment; which is the maximum gripping force that the Baxter robot can exert (Rethink Robotics, 2015b). From the FEA results I was able to see factor of safety for the model was at maximum 15, however had a minimum of 2.199, with the max stress, strain and displacement being 9.094Mpa, 0.1321 and 5.972mm respectively figure 12. The data provided by the FEA highlighted that the internal corner of the end effector was causing a weak point within the model and whilst a factor of safety of 2.199 means that the model would be unlikely to break and have a critical failure under the maximum force of the Baxter’s grip strength, for safety and unforeseen events such as an external force I would prefer the degree of safety to be at least a factor of five for the entire model (The Engineering ToolBox, 2010). There I decided to make alteration to the design to ensure that it was structurally safe.

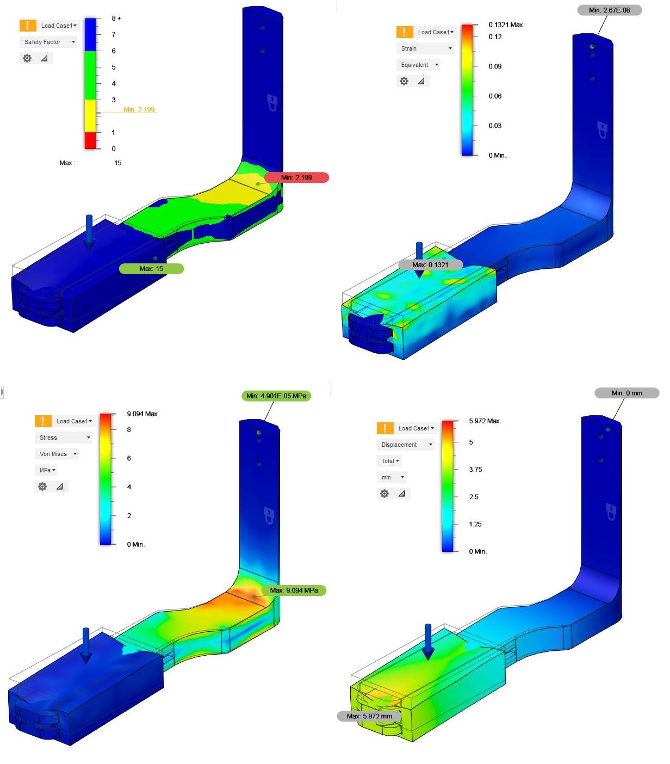
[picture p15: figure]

Figure 12: FEA ABS 35N Initial Design

With the weak points of the model identified, I made several changes to the models. Firstly, I increased the size of the fillet in the internal corner of the end effect and added an additional fillet to the external corner of the model. I decided to do this in order to distribute the force acting on the corner over a larger surface area, which will strengthen the weak point within the model, allowing a greater force to be exerted without failure. Secondly, I also increased the thickness of the gripper portion of the end effector by 1.1mm in both directions. The additional material will once again strengthen the weak points by having more material to distribute the force being applied figure 13.

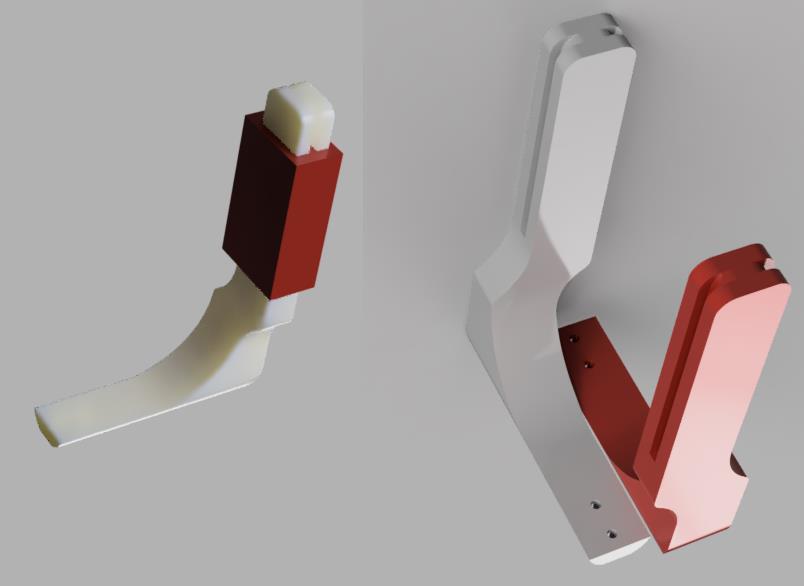
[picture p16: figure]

Figure 13: End effector Final Design

With the refined design completed, I then went on to carry out another series of FEA tests. For the tests I used the same constraints, materials, and loads as the previous FEA study. With alterations of the design in place the new minimum factor of safety for the ABS model is now 5.501, which is an improvement from the previous design and meets the standard that I wanted to achieve. The max stress, strain and displacement being 3.636Mpa, 0.01822 and 1.149mm respectively figure 14. Once again from the FEA we can see that the weak point within the model is still the internal corner, however I have been able to successfully strengthen it, to meet the structural requirements set. From the data we can see that the model has improved in all aspects of the FEA, the stress being almost a factor of three times smaller, which concluded that the force has been distributed around the model in a more structurally efficient manner. Whilst the adjustments to the model do mean that the material cost will increase and that the overall model is a more bulky and less streamlined than it previously was, the model is still fully printable which means that the end effector can still be printed and replaced if needed in the future at the University at a low cost.

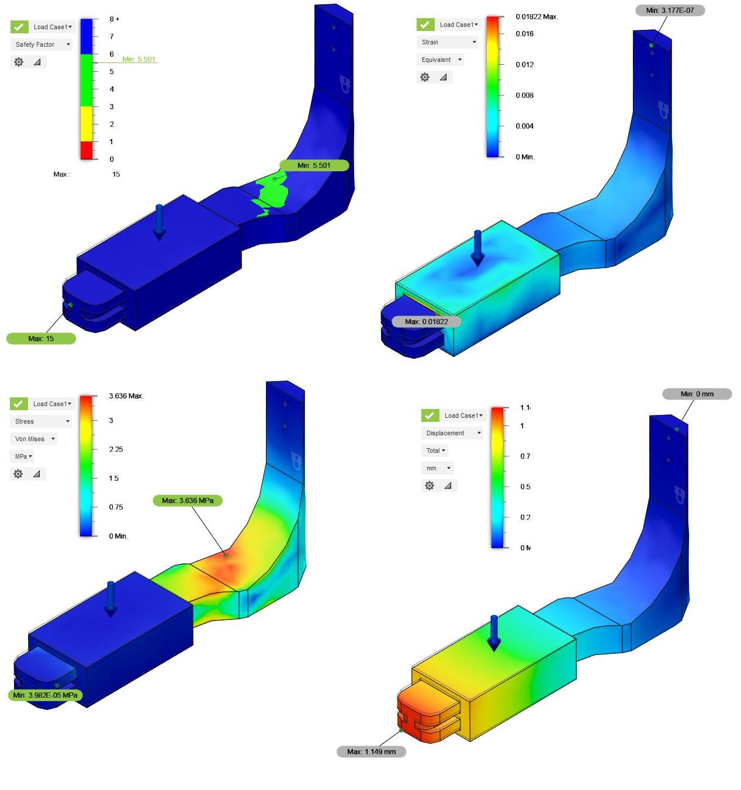
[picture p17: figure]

Figure 14: FEA ABS 35N Final Design

As a final experiment I wanted to conduct an additional FEA test, on the initial model to discover if the model would be able to achieve the structural requirements if another material was used in place of ABS. For this test I decided to conduct the study using aluminium, which has a Young’s Modulus of 69Gpa (The Engineering ToolBox, 2003), which is larger in comparison to the Young’s Modulus of ABS, previously stated as 1.1-2.9Gpa (igem, 2015). With the material selected a new FEA study was conducted using the same constraints and load of 35N and the results concluded that the new minimum factor of safety is now 15, which is around three times higher than the factor of safety when using ABS as the material. The results also state that the max stress, strain and displacement being 9.79Mpa, 0.01401 and 0.1766mm respectively figure 15. Whilst the results do provide confidence in the initial designs ability to meet the structural requirements to withstand the maximum force of Baxter gripper (35N), with a factor of safety being above five, the manufacturing process is now more complex. With the use of materials such as ABS and PLA the model would be able to be manufactured at the University by method of 3D printing. With this method of manufacture, a new print of the model would be very easy to achieve and very cheap. Due to the method of 3D printing there is very little waste product; with most of the waste being structural supports to aid the printing process. However, in order for the aluminium gripper to be manufactured, the model would have to be machined from a larger piece of aluminium, which produces a high volume of waste product and thus drives the cost up for the model to be produced. Overall, both designs show promise and have confidence in their abilities to withstand the required forces, dependent on their material of manufacture. Part of my goal for the design of the replacement end effector for the Baxter robot is that, if required a new replacement could be readily produced in the future, therefore I believe that the best material to base the design around is PLA and ABS, as it would make the manufacturing inexpensive. The main advantage of the aluminium model is that it provides a higher level of protection for the end effector against external forces which could be greater than 35N, however a key point to consider is that it is preferred that the easily replaced gripper is broken when exerted under extreme forces, than for the gripper to survive but for Baxter to break in its place.

Model | Material | Minimum Factor of Safety | Max Stress (Mpa) | Strain | Displacement (mm)
Initial (ALU Model) | ABS | 2.199 | 9.094 | 0.1321 | 5.972
Initial (ALU Model) | Aluminium | 15 | 9.79 | 0.01401 | 0.1766
Final (ABS Model) | ABS | 5.501 | 3.636 | 0.01822 | 1.149

Table 2: Data from FEA Testing

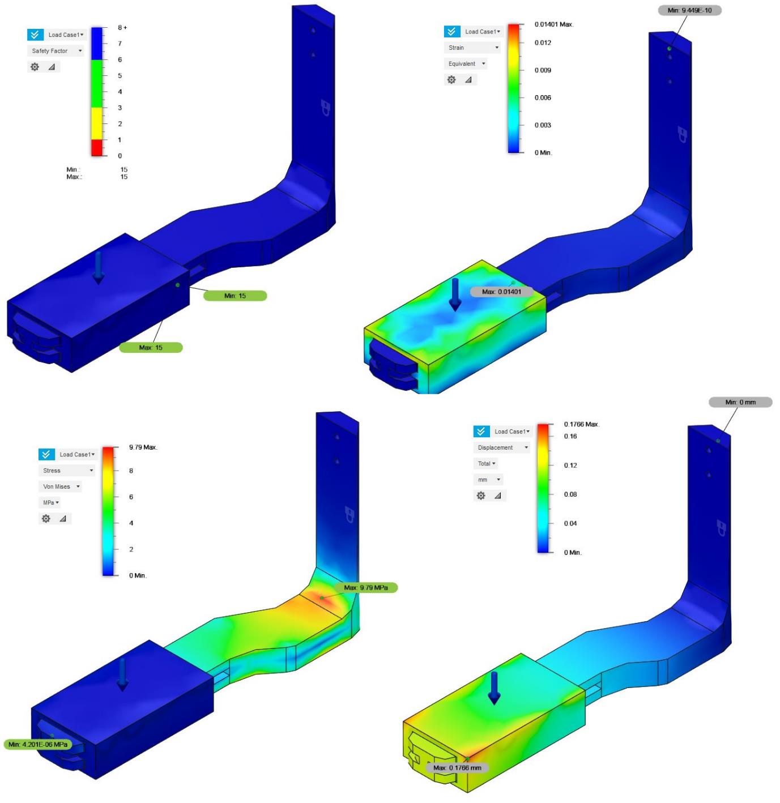
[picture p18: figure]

Figure 15: FEA ALU 35N initial design alternative material

### 4.2 ROS Gazebo 7 Simulation of Baxter

Alongside physical repairs one of my goals was to provide a digital workstation and coding framework, which would allow future research to be carried out using the Baxter robot at the University of Plymouth. I chose to base the workspace around using ROS (Robot Operating System), as ROS is a standard framework within the field of robotics for writing and sharing software (ROS, 2020). In addition, Rethink Robotics also provided a toolbox to control and operate the Baxter robot, upon its initial release. Rethink Robotics provides a manual to set up the workstation to control the Baxter robot (Rethink Robotics, 2015c), with software that was released in 2012 and last updated in 2015. The current software and documentation are using legacy versions of both Ubuntu 14.04 and ROS Inigo, which means that this software (without changes) is not compatible with the University’s software setup, which uses Ubuntu 16.04 and ROS Kinetic.

Due to the University’s laboratories being shut because of COVID-19, my research was carried out at home using a VMware Workstation running a 64-bit boot of Ubuntu 16.04 with the specifications shown in figure 16.

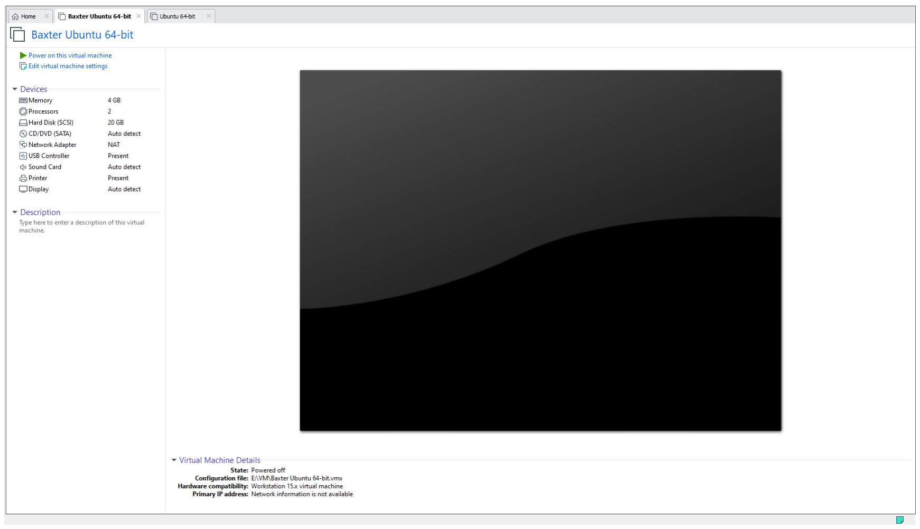
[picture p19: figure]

Figure 16: VMware Workstation setup for 64-bit Ubuntu 16.04

With a standard install of ROS Kinetic installed and a workspace created, the code in figure 17 downloads Rethink Robotics’ SDK for the Baxter robot from their GitHub repository.

Figure 17: Code to install Baxter SDK

Once the SDK has been downloaded, we need to next compile the workspace, which is achieved by using the catkin_make command in the terminal figure 18.

Figure 18: Compiling the workspace

After the workspace has compiled, we next need to configure the baxter.sh file with the parameters of the current workstation figure 19.

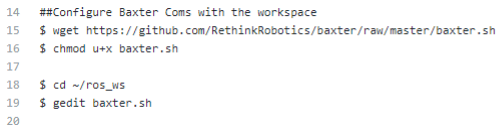
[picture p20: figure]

Figure 19: baxter.sh

In the baxter.sh file, in order for the workstation to be used within a simulation the baxter_hostname has to set to “my_computer.local”, however if the user wants to interact with the physical Baxter robot rather than the simulation, the variable “your_ip” needs to be set to the workstations ip address. Additionally, the variable of ros_version, needs to be set to “kinetic” in order for the software to work with the correct version of ROS figure 20.

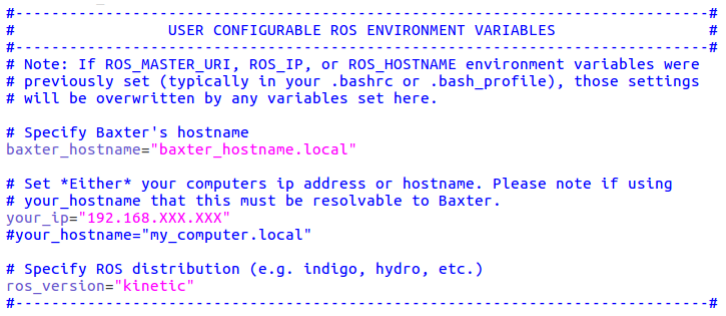
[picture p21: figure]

Figure 20: Configuration of ROS Environment Variables

With the workstation now setup, Rethink Robotics’ Baxter simulator can now be installed. Rethink Robotic provide a manual which is compatible with ROS kinetic and therefore no changes need to be made from the original documentation (Rethink Robotics, 2015d). The Baxter simulator uses gazebo 7 as its simulation environment and in order to run the software the accelerate 3D graphics option needs to be unticked on the virtual machine settings figure 21.

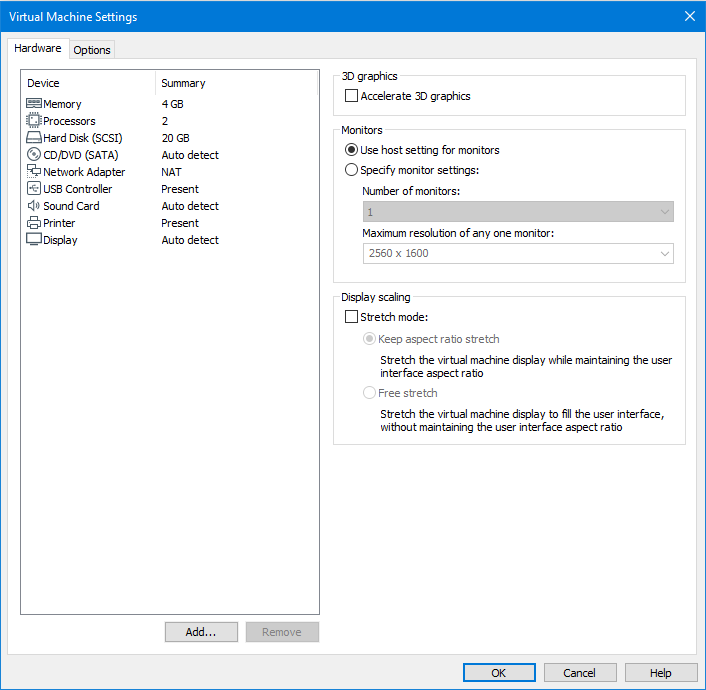
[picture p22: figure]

Figure 21: Virtual Machine Settings for Gazebo 7

As a default the simulator comes with a repository of a few prewritten test programs that Rethink Robotics have provided which allow the user to test and interact with Baxter within the simulation. One of the programmes, joint_position_keyboard.py allows for the user to control each one of the Baxter robots’ servos (including the gripper) by entering keyboard inputs into the command terminal. This then increments or decrements the value of a joints position by a fixed amount and is shown on the full model of Baxter within the Gazebo 7 environment figure 22. With the framework of this programme a study could be conducted to have the user interact with the Baxter robot to run a simple pick and place exercise. Another programme that was used was a joint velocity wobbler programme in combination with the joint position controller, which had the Baxter robot, move its servos in random direction, whilst the measuring the steady state errors, with the steady state error being the difference between the input signal to the system and the resultant output of the system. This allows the user to test the robot in order to tune the feedback controllers that’s being used with the simulation by adjusting its values, to achieve more accurate results when positioning the arms (figure 22). This could be further experimented with by adding a random value as an input to observe how the PID controller would handle an error. With these observations made, the PID controller could be tuned to be able to respond effectively to the steady state error of the arms movements. Whilst the steady state error can be simulated, experiments using the real Baxter robot would still be required to calibrate the PID controller as the error caused by each servo will differ from the random input style error generated to test in simulation.

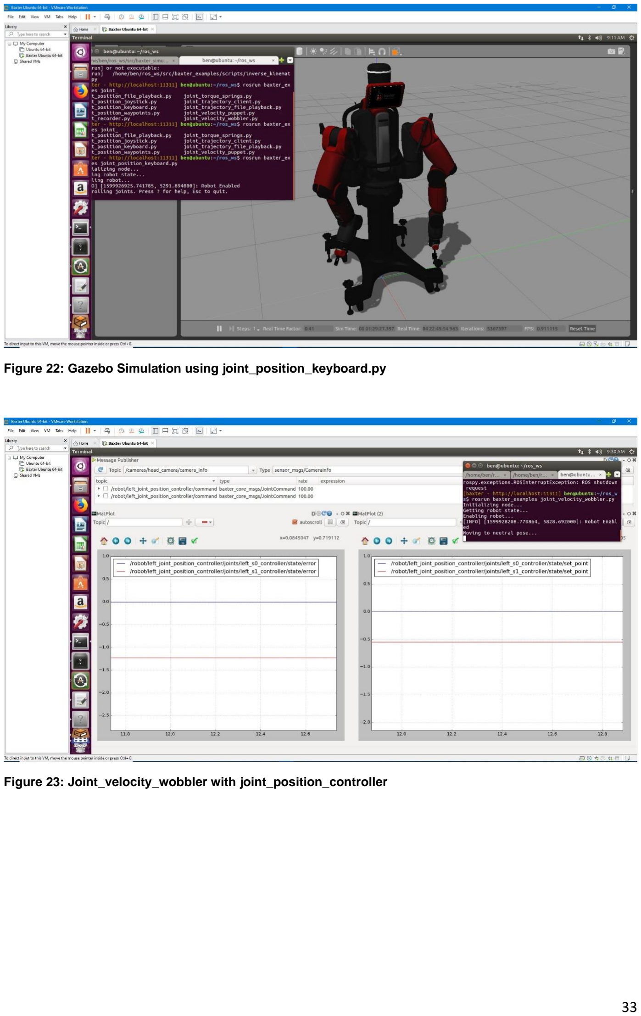
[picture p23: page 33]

Figure 22: Gazebo Simulation using joint_position_keyboard.py

Figure 23: Joint_velocity_wobbler with joint_position_controller

### 4.3 Semaphore Signalling

After establishing that the Gazebo simulation was set up and operating correctly, I started to create my own piece of software that would allow a user to operate with the Baxter robot. The concept of the programme was to implement a similar style of interaction seen in the joint_position_keyboard.py test programme, however this time when the user enters a letter using keyboard inputs it would set Baxter’s joint angles of his servos in his arms a pose that would represent the letter as a semaphore signal. Semaphore signalling is a system designed by the Chappe brothers in the 18th century (Centre of Innovation in Mathematics Teaching, 2006) and is a method of using two flags to signal letters by the position of the user’s arms when holding the flags. However due to performance issues and complications with the Gazebo simulation I decided to carry out the simulation using MATLAB instead, which was partially because I was able to integrate the programme with the rest of the project and also because the MATLAB simulation was more stable that the Gazebo simulation. Despite the change in software, the principle and application of the concept remains the same.

The MATLAB programme follows the same principle, the user has the option to enter the characters of Baxter’s name into the command window of MATLAB. If a correct key is pressed, Baxter positions his arms to represent the corresponding semaphore signal. This is achieved with the use of the forward kinematics, established earlier in the project. A demonstration of this can be seen in figures 24-29.

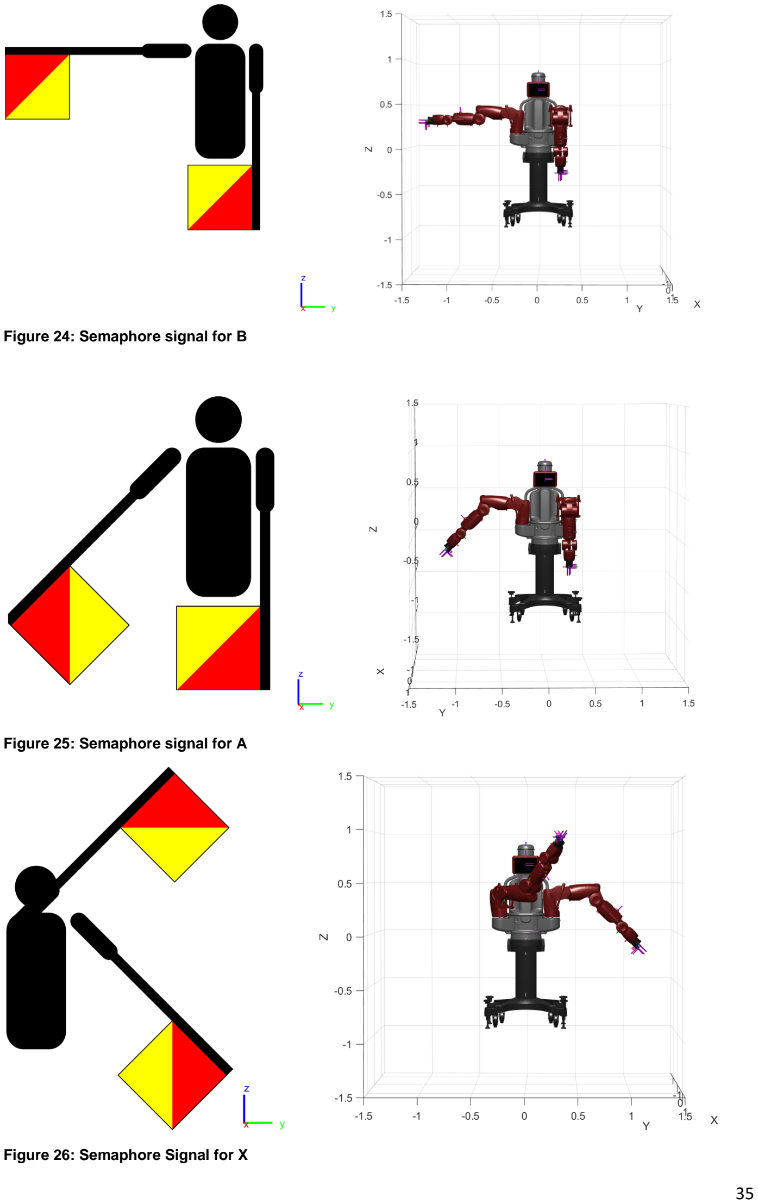
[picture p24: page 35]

Figure 24: Semaphore signal for B

Figure 25: Semaphore signal for A

Figure 26: Semaphore Signal for X

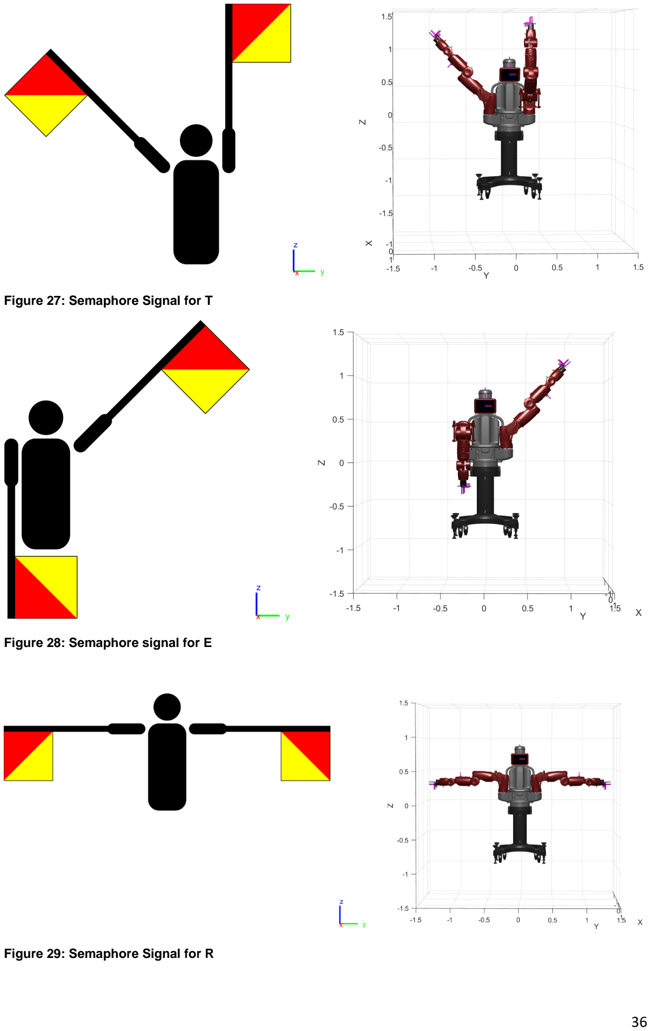
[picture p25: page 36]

Figure 27: Semaphore Signal for T

Figure 28: Semaphore signal for E

Figure 29: Semaphore Signal for R

## 5. Discussion and Analysis

### 5.1 CAD

The design for the replacement end effector offered two different varieties depending on the material selected, with the options being 3D printable PLA/ABS or machined aluminium. Both of the designs are relatively similar, with the main difference being that the PLA/ABS design has more material on the base of the gripper that would be attached to Baxter and a longer fillet on the bend. The reasoning behind these additions to the original design (aluminium variation), is to provide a better distribution of force along the bend. Without the additional material the minimum factor of safety with a force of 35N applied, was only 2.199, whereas with the changes it was 5.501, which is achieved the standard that I wanted to achieve in order to provide a piece of equipment that was structurally stable to be used rigorously without concern of breaking. Additionally, the minimum factor of safety for the aluminium design with the same constraints and forces applied was 15, which more than exceeds target factor of safety of 5.

In addition to the added cost of machining a piece from aluminium in comparison to 3D printing one, another drawback could be the aluminium designs hight factor of safety, which means that the end effector could theoretically suffer an external impact force of up to 525N before catastrophic failure of the part. Whilst providing a structurally strong and stable part of a certain quality is important so then the grippers of the end effector will not require constant replacement, it is also important to consider the forces that would be applied to the rest of the robot if the end effector experiences a large impact force. With the Baxter robot’s servos costing more than a replacement gripper it is perhaps best to design the gripper to break at a predetermined threshold, which would allows for the gripper to be used within normal operation without issue, but would break when experiencing extreme force, in order to protect the servos and their gear boxes. With that in mind the PLA/ABS design may be the better design, but both designs have their benefits and drawbacks.

Whilst the PLA/ABS design is cheaper to produce it may not be the best material choice for some situations. For example if you wanted to use the Baxter robot to carry out research into cooking robots, the high temperature of objects within that environment that Baxter would be interacting with may cause the end effector to take damage due to the heat melting part of it, with the print bed temperature being around 72⁰C for PLA (igem, 2015). Due to the environmental elements surrounding this particular task, the end effector using the aluminium grippers would be better suited over the 3D printed PLA/ABS alternative.

With the two iterations of the grippers both achieving all of the design requirements to ensure the end effector will be functional, they both require physical testing with the actual Baxter robot, before I can say for certain that the design is finalised and without any major faults or oversights. Due to the COVID-19 Pandemic, I was not able to gain access to the Baxter robot at the University of Plymouth throughout the process of the project which meant that the parameters that the for the gripper were obtained from partially from data sheets and other reference images and materials, therefore a few parameters may need to be fine-tuned once access to the Baxter robot to obtained. The main concern is the alignment of the base, whilst the grippers have been designed to work smoothly in a pair to provide a vice like gripper action, the screw holes may need to be adjusted, which could cause the need for an modification to the base to be made.

### 5.2 Kinematics

The kinematics derived and demonstrated within this project show examples of both forward and inverse kinematics. For the purposes and scope of the project the kinematics are purely theoretical and demonstrated in a perfect system, and therefore don’t fully represent a real system. In a real system, such as using the kinematic model with the physical Baxter robot, the servos would not be perfect and therefore the location of the end effector within a 3D plane may experience some compound drift. Due to experiencing drift the certainty of the position of the end effector would decrease, however a solution to this could be solved by the use of a closed loop feedback control system. The implementation of a closed loop feedback control system can be used to increase the accuracy of the end effector by providing feedback data which will allow for adjustments to be made to the joint angles of the servos to reach the required goal. Several methods could be used as a solution this issue including a simple proportional-integral-derivative controller (PID controller) or a Kalman filter.

With the forward kinematics the model of Baxter within MATLAB could be successfully implemented to calculate the pose of the Baxter robot using the joint angles as a control input. The method of forward kinematics is well suited for manual control of the Baxter robot, which would be ideal for situations where the user would be controlling the robot via teleoperation. Whilst in the MATLAB programme the joint angles need to be inputted using a keyboard, control of the joint angles could be provided by the use of a controller that would allow the user to increase and decrease the value of the joint angles, whilst providing an easy way for the user to switch between the selected joint to interact with. With a human operator controlling the robot, there is less requirement for a closed loop feedback controller, as the operator is acting as such system.

Similar to the forward kinematics, the inverse kinematics were also successfully demonstrated using a model of Baxter with MALAB, with the user imputing the target coordinates. Inverse kinematics are useful when integrated with an autonomous system, as they allow for the user to input the target location of the end effector and for the robot to provide a solution for the joint angles. However as discussed, over or undershoot may provide an issue when using an open loop system with forward kinematics, which is why a closed loop feedback system preferred to maintain accuracy.

### 5.3 Interaction

The interaction element of the project was originally focused around using the Gazebo simulation of the Baxter robot in ROS, with the idea of having Baxter carrying out semaphore signalling. However, the semaphore signalling interactive programme was instead carried out in MATLAB using the forward kinematic model that I had implemented earlier in the project. Whilst in the programme Baxter can carry out the required gestures to spell out his own name using semaphore signals, he does not currently use signalling flags to properly convey the message. With access to Baxter, further research could be carried out with Baxter interacting with a set of signalling flags, where a project could be centred around using Baxter as a translator from variable or written commands to semaphore signalling. It is also possible that with the use of computer vision that Baxter could be taught to read semaphore signals, to then be used as input commands. In order to do this Baxter would need to make use of RGB-D camera to track the skeletal data of a user which could then be used with a machine learning programme to match the data with predetermined poses (Win, S. et al., 2020).

In addition to the semaphore signalling programme, experiments were also carried out using the Gazebo 7 ROS simulations using Baxter to test some of the programmes provided by Rethink Robotics. This included being able interact with Baxter with the use of keyboard inputs that would change his joint angles and the joint velocity wobbler programme in combination with the joint position controller. Whilst the experiments provided detailed visuals of the Baxter robot operating, the simulation experienced a large amount of lag, which is believed to be caused by the virtual machine not having the required resources to run a resource heavy simulation. To confirm this further testing will be required in the University’s labs, where the computers are better suited to carry out such a task. Alternatively, the software is quite old and a new alternative simulation environment, such as v-rep may be beneficial.

### 5.4 Literature and Teaching

From the literature review it became clear that Baxter still has a lot to contribute towards research, especially within the field of robot-human interaction. Whilst the literature covered was broad in scope, it highlighted the fact that Baxter has a lot of potential outside of the usual tasks and operation usually associated with the robot, which are usually industrial based. With the Baxter robot having a lot of potential research opportunities into different field, it’s creates a valuable platform to use to teach a variety of different practices within robotics. Besides having the ability to aid the teaching of kinematics and forces, Baxter provides an opportunity to learn about human-robot interaction alongside the interaction of tools, equipment and objects. Due to the nature of the subject this would then require knowledge and application of computer vision systems, machine learning, control theory, neural networks, alongside the understanding of coding in software such as MATLAB and ROS. Therefore, because of the versatility of the Baxter robot, he can be valuable resource for research and teaching purposes.

## 6. Future work

Beyond this project I would like to further explore different areas of research using the Baxter robot. With the laboratory open again I would like to carry out physical testing on the real Baxter robot using both the grippers and kinematic models. I would also like carry out experiments to test the accuracy of the Baxter robot. To do this I would use the robotic toolbox in MATLAB to generate a trajectory for Baxter to follow, which could be applied to both simulation and physical robot. With these tests I can record the position data for the arms in their end positions, which can be used to evaluate the accuracy by making a direct comparison between the two results.

Additionally, to calibration tests I would also like to carry out a series of projects using the real Baxter robot. Firstly, I would like to continue to work with the Baxter robot to further the semaphore signalling system that has been developed within the project. In a future study I would like to train the Baxter robot to recognise a semaphore signal and to be able to repeat the signal. This would be achieved with the use of a depth camera which could be used to carry out skeletal tracking of a human producing the signals. With the skeletal data recorded, the data could be converted to forward kinematics for Baxter to replicate to reproduce the same signal. Baxter could also use the values of the joint angles to determine the identification of the semaphore signal, which would allow for him to translate the signal. A similar experiment was carried out using the pepper robot by Tian, N. et al., (2018), where they used cloud computing to mirror semaphore signals.

Another project that I would also like to pursue would be the use of Baxter as a cooking robot, that could be used within an industrial or home environment. For a robot to be capable to perform a cooking task autonomously, computer vision will be a key tool to achieve its goal. In a study carried out by Ikegami, N. et al., (2020) they investigated methods of cutting objects within the kitchen environment. In order to achieve this goal, they implemented an EMD Neural Network to train the robot to carry out a cutting action depending on the desired result. The robot used an Xbox Kinect camera to provide 3D image data of the environment that the robot would be operating in, this sort of set up can be seen in multiple different studies using the Baxter robot include one carried out by Avalos, J. et al., (2017). Whilst the research was carried out only in simulation, the results show promise that this method could be applied to a real-world robot, given similar shaped objects to cut. Additionally, in a study carried out by Zhu, Q. el al., (2017), the ARMAR-III kitchen robot created by the Karlsruhe Institute of Technology (Robots IEEE, 2020e) was used to carry out research which was mainly focused on a verbalisation system for the robot to recognise what task it was carrying out and to convey a concise report. The activities that the robot would complete would include mixing, pouring, wiping, along with kitchen-based pick and place interaction, which was achieved due the use of the robot’s stereo vision. Once again with an Xbox Kinect camera fitted to Baxter, research into cooking and kitchen application for Baxter are achievable. Lastly in a study carried out by Junge, K. et al., (2020) and RGB-D camera was used alongside a Bayesian filter in part of a feedback system which would allow a robot to cook a perfect omelette by using the RGB data to achieve the desired result.

Due to Baxter’s compliant joints and with the use of torque sensors, which allow him to work safely with humans, Baxter would be an interesting robot to carry out cooking related tasks. Whilst with machine learning and neural network application, Baxter could be programmed to complete kitchen tasks autonomously, Baxter could also be controlled via teleoperation to allow a user to carry out kitchen an external environment. This could be used in combination with a VR headset, which can be seen achieved in a study by Lipton J.I. et al., (2018) which would allow the user to see the environment from Baxter’s perspective. The user could then make suggestive movements using VR controllers in combination with Baxter’s torque force sensing to ensure that the appropriate force is being used to carry out a task such as cutting vegetables or gripping a saucepan.
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

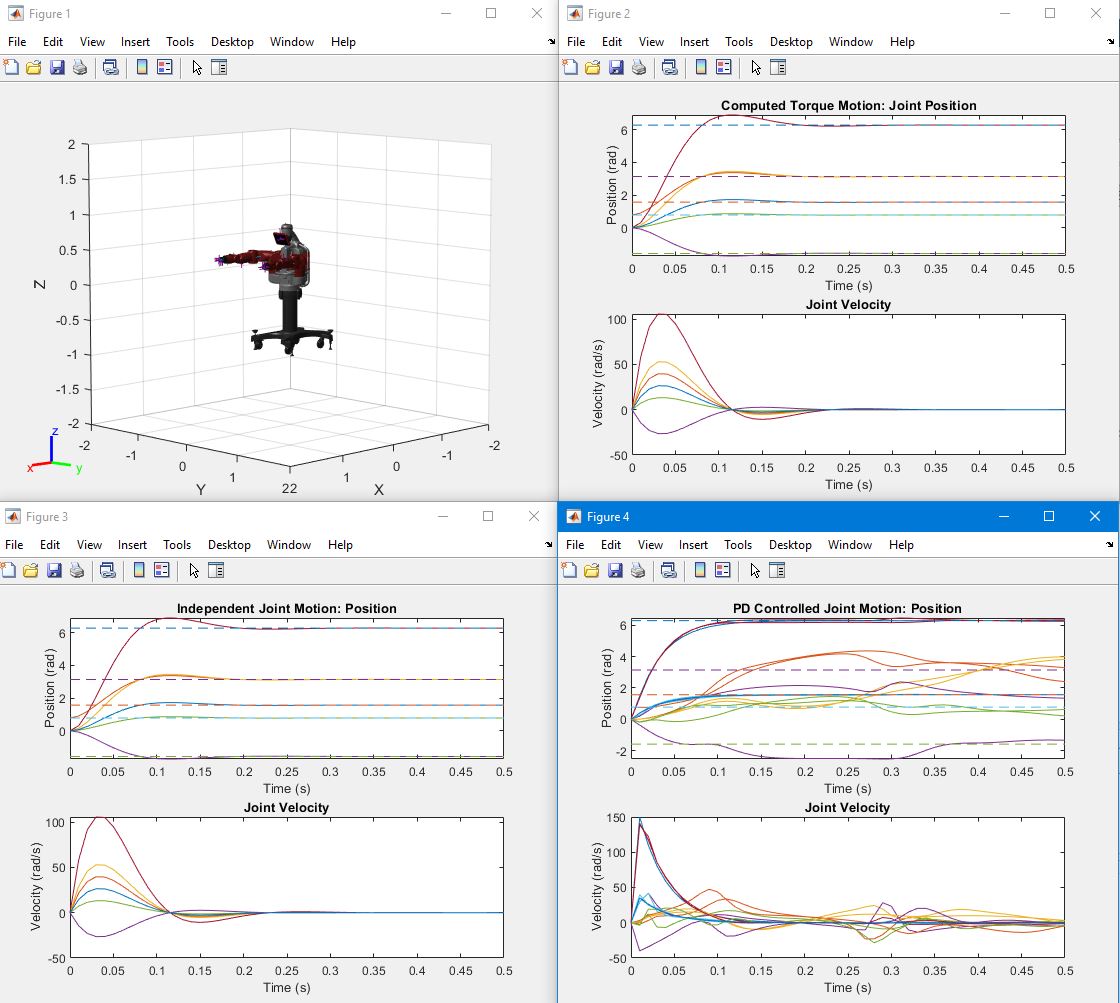
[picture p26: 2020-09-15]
Pictures/Kinematics/Trajectory_Generation_2.JPG

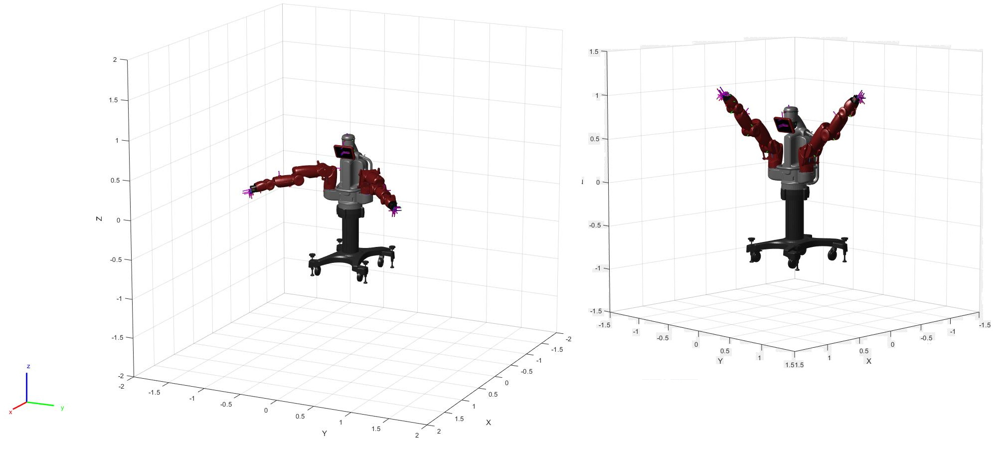
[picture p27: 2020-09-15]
Pictures/Kinematics/Forwards_kinematics.png

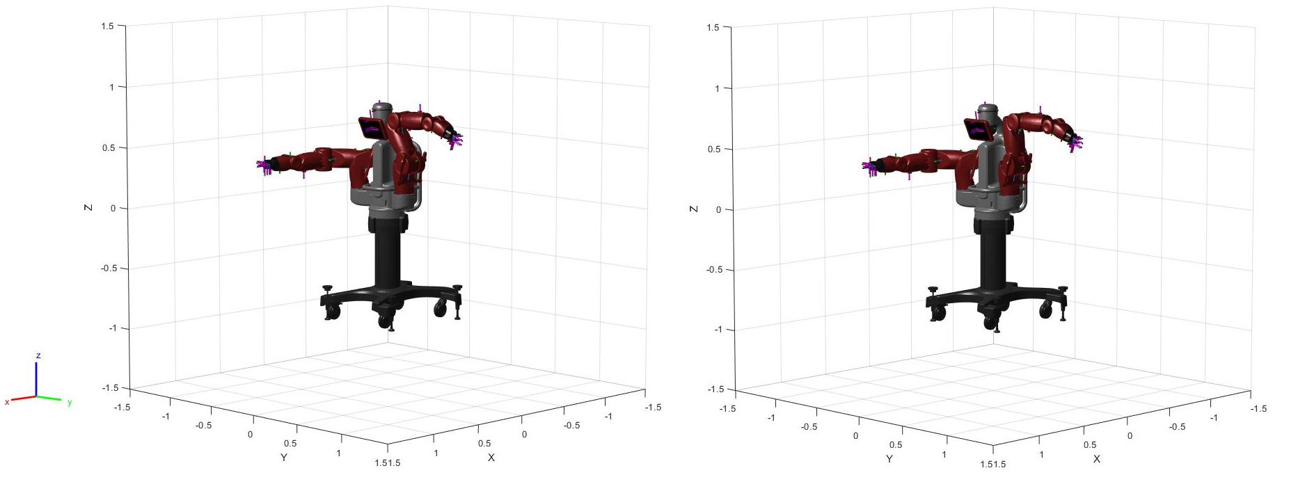
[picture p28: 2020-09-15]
Pictures/Kinematics/Inverse_kinematics.png

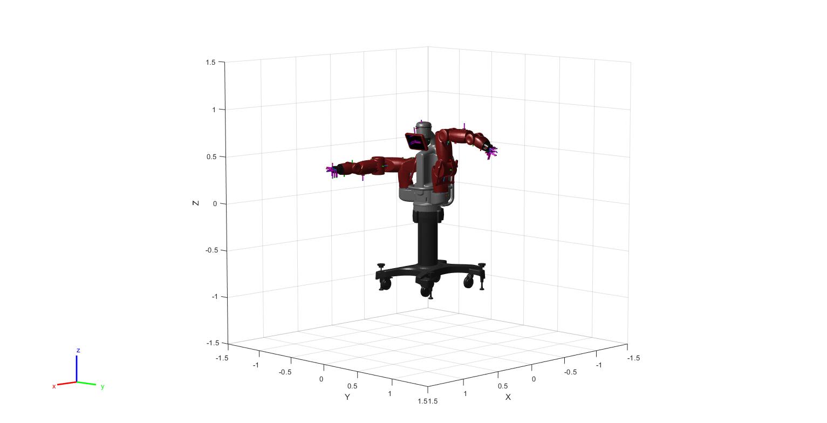
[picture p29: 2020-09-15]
Pictures/Kinematics/Inverse_Finish.jpg

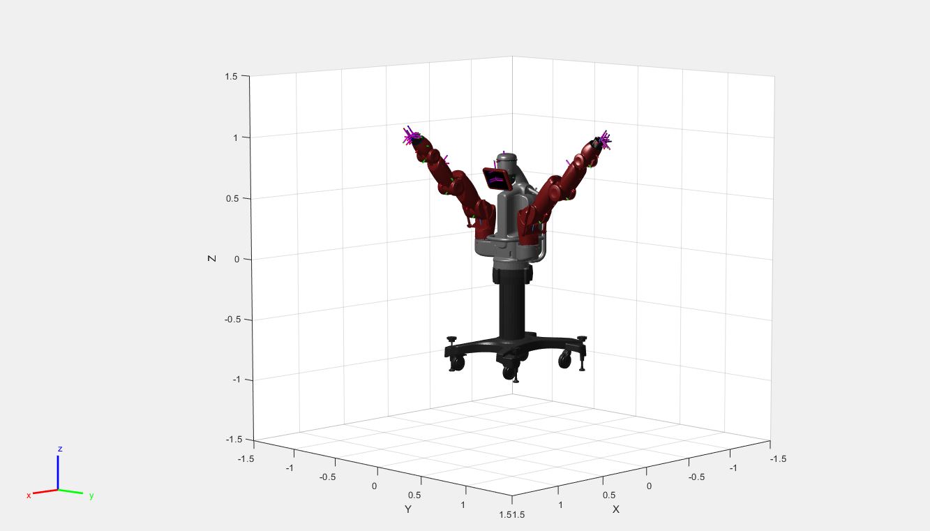
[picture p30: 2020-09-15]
Pictures/Kinematics/Forwards.JPG

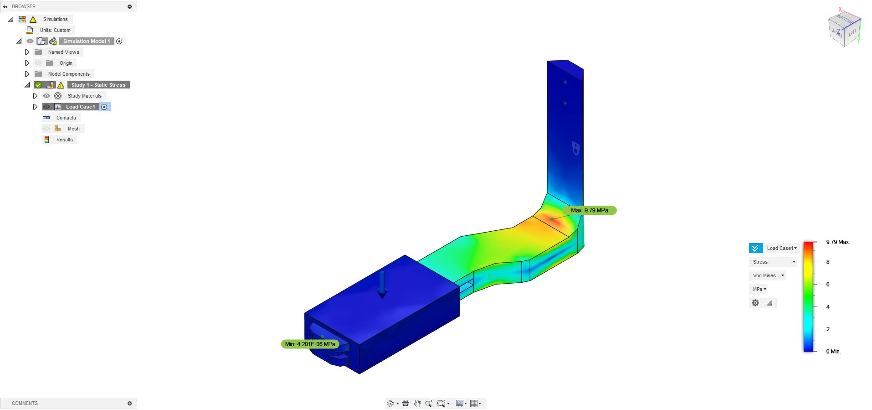
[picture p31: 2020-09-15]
Pictures/CAD/Aluminium/Stress.JPG

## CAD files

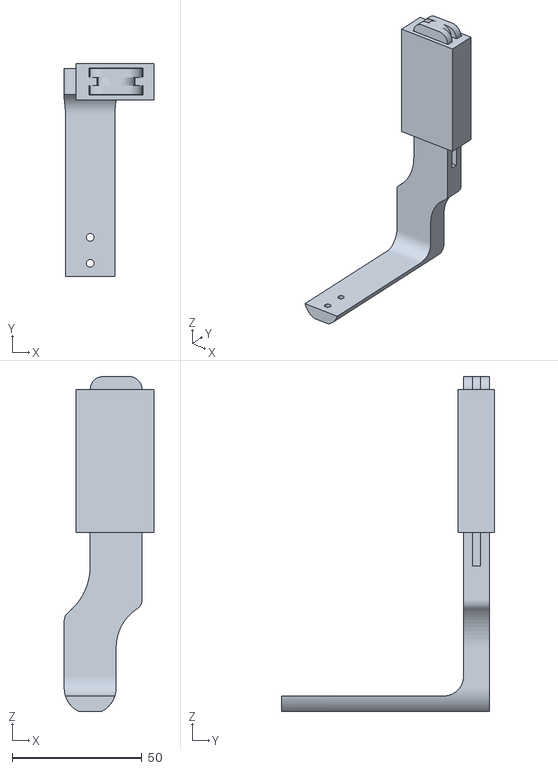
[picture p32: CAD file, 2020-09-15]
CAD/ALU_STL.stl
34.5 x 81.9 x 129.0

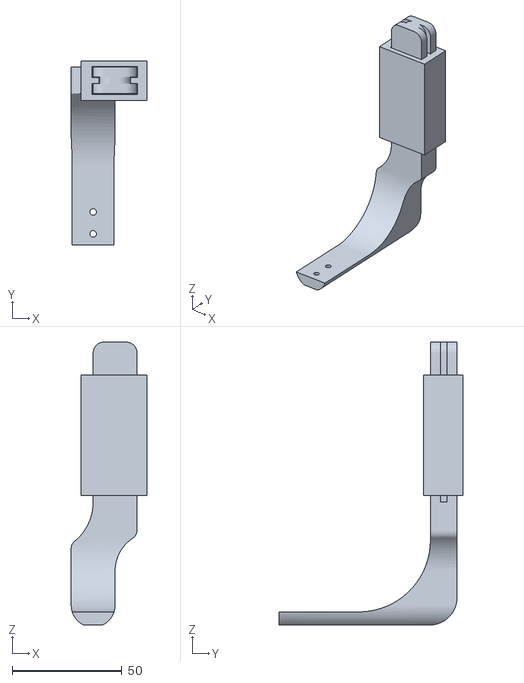
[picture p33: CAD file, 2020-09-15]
CAD/ABS Design.stl
34.5 x 83.7 x 129.0

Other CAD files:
CAD/ABS Design.f3z
CAD/ABS Pair.f3z
CAD/Aluminium Design.f3z
CAD/Aluminium Pair.f3z
CAD/Baxter Project.f3d
CAD/Gripper II v13.f3d
CAD/Gripper III v16.f3z
CAD/Gripper Sponge v9.f3d
